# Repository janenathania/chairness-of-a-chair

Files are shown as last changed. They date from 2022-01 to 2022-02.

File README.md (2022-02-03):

# CHAIRNESS OF A CHAIR
## Hochschule Augsburg - Interactive Media - 5th Semester - Wicked Things

This repository contains source of codes and informations about the hardwares and its hacking. Everything that is needed to hack a hoverboard and control it with Arduino and Processing to make a fully functional remote controlled moving chair can be found here. Some codes and methods are taken from other GitHub Repositories as well, the link will be provided in in the description.

## TABLE OF CONTENT
- [HARDWARE](https://github.com/janenathania/chairness-of-a-chair/blob/main/README.md#hardware)
- [FLASHING](https://github.com/janenathania/chairness-of-a-chair/blob/main/README.md#flashing)
- [SERIAL INTERFACE](https://github.com/janenathania/chairness-of-a-chair/blob/main/README.md#serial_interface)
- [ARDUINO](https://github.com/janenathania/chairness-of-a-chair/blob/main/README.md#arduino)
- [PROCESSING](https://github.com/janenathania/chairness-of-a-chair/blob/main/README.md#processing)
- [PROTOTYPE](https://github.com/janenathania/chairness-of-a-chair/blob/main/README.md#prototypes)
- [3D PRINT](https://github.com/janenathania/chairness-of-a-chair/blob/main/README.md#3d_print)

## HARDWARE

For this project we use the older version of the hoverboard that only has one chip to control both side of the hoverboard.
The main model of the chip is STM32F103. 

 

Further information and instruction can be found in a GitHub Repository by lucysrausch <br/>
https://github.com/lucysrausch/hoverboard-firmware-hack

## FLASHING

In order to control the hoverboard we have to hack the firmware first. Fristly we have to erase every progamms that are built in the hoverboard.
The method is called flashing. There are several methods to do the flashing

We follow the whole procedure from this website <br/>
http://bauhausinteraction.org/opl/how-to-control-a-hoverboard-with-an-arduino/

And more detailed instructions can be found from this GitHub repository
The Method that we follow to make this project is `VARIANT_USART` <br/>
https://github.com/EFeru/hoverboard-firmware-hack-FOC

## SERIAL INTERFACE
### ESP Code

Parts used:
- Hoverboard with STM32F103 chip
- ESP8266
- DC/DC Converter
- Wireless Router (we use tp-link TL-MR3020)

If you are using a ESP for the first time, follow these instructions to get ready to use it: https://randomnerdtutorials.com/how-to-install-esp8266-board-arduino-ide/

Then import these two libraries to your Arduino IDE:
- Ramp for motors https://github.com/siteswapjuggler/RAMP
- Protocoll for wireless communication between Processing and ESP https://sojamo.de/libraries/oscP5/network

You need a Wireless Router with an AP Mode. In the Code you have to change the SSID and PWD into your own password for the router
If you are building two chairs like us, you might have to change the last digit of the IPAddress for the second ESP
Each Chair requires 1 ESP and the IPAdress should be different from each other

`const IPAddress ip(192, 168, 1, 202); change the 202 to 203.`



After that you can upload our ESP-Code to your ESP. 

### ESP Build

Disconnect the Sideboard which is on the side of the mainboard. Take your ESP and DC Converter and connect everything like this:
- 15V red wire goes to the left wire of the converter, which is labeled with `in`
- TX blue wire goes to the RX pin of the ESP
- RX green wire goes to the TX pin of the ESP
- GND black wire goes to the middle wire of the converter with the `ground` label
- connect another black wire to the middle wire of the converter and put it on the GND pin on the ESP
- the last wire of the converter (adjust 5V out) goes to the Vin pin of the ESP 



Original Links of the images <br/>
- https://m.media-amazon.com/images/I/51Z9NoCxWwL._SL1000_.jpg
- https://wiki.volkszaehler.org/_media/hardware/controllers/amica-nodemcu-esp8266-lua-cp2102-wifi-development-module-iot-gujarat.png
- https://github.com/EFeru/hoverboard-firmware-hack-FOC/blob/master/docs/pictures/mainboard_pinout.png

## ARDUINO

Parts used:
- 1x Arduino Uno
- 1x Seedstudio Grove Shield
- 2x Seedstudio Grove Joystick

Our Code is able to steer two hoverboards at the same time.

We used an Arduino Uno with the Seedstudio Grove Shield on top and we connect the first Seedstudio Grove Joystick to the A0 and the second Joystick to the A2 Connector of the Grove Shield.

We send the coordinates of the Joysticks as a string over the serial port.

GitHub Repository from HybridThingsLab <br/>
https://github.com/HybridThingsLab/wicked-things-2021/tree/main/01_playground/Arduino

## PROCESSING

Processing is able to read the data from the Arduino and send it over WLAN to the ESP.

To make sure that everything is working correctly you need use Processing 4 as the software.

Open the processing code (that you can find in the folder above) and connect your arduino to your pc. Run the code and check if there is an error. If so that means the code uses the wrong usb port. Check the number of your port on which your arduino is connected to and change it in the code.



If there are two squares and you can move them with the joysticks, then everything is working fine.

Now start the hoverboard and connect the Wlan of your PC with the Router and run the processing code .

If everything is correct, your hoverboard should move if you use the joysticks.



GitHub Repository from HybridThingsLab <br/>
https://github.com/HybridThingsLab/wicked-things-2021/tree/main/01_playground/Processing

## PROTOTYPES

To ensure that the chair is safe to ride we have done some experiments on the shape of the chair and the supporting board the is built between the hoverboard and the actual chair.

  

The board acts not only as a support that connect hoverboard and the chair, but also as a place to put the motherboard that control the whole thing.

  

The final design of the chair. The shape of the chair is chosen after several user tests to decide which shape is the safest to ride on. The important feature of the moving chair is its backrest. It is to protect the user from falling over during sudden movement of the chair.
The board at the bottom is made quite broad. It is made like that to make sure that the user has enough space to place their feet on it and feel sturdy while sitting on the chair. The board itself has in total 5 wheels. 2 wheels are from the hoverboard that can move following the controllers input and the other 3 wheels are the supporting wheels (2 in front and 1 at the back) to make sure that the whole chair doesn't flip over during sudden movement or sudden break.

## 3D PRINT

This is our extra parts. We make the cover for controllers, Arduino and ESP with 3D Print. You can make it with anything you like. But we attached the raw files of the 3D Models so you can try to 3D Print it if you have a 3D Printer.

  

The controller are made main from an arudino joystick kit and it is covered with a 3D printed cover. To make it a cleaner look and more rigid body. It makes the controller easier to hold it and comfortable while using it, so that the controllers can controll the chair precisely. <br/>



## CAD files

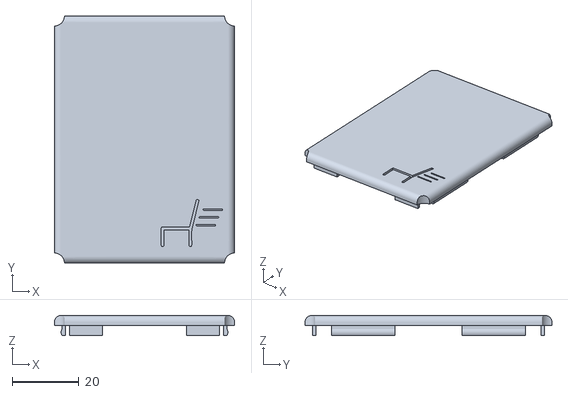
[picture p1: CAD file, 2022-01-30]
3D Print/esp_box_deckel.stl
54.0 x 74.0 x 6.00

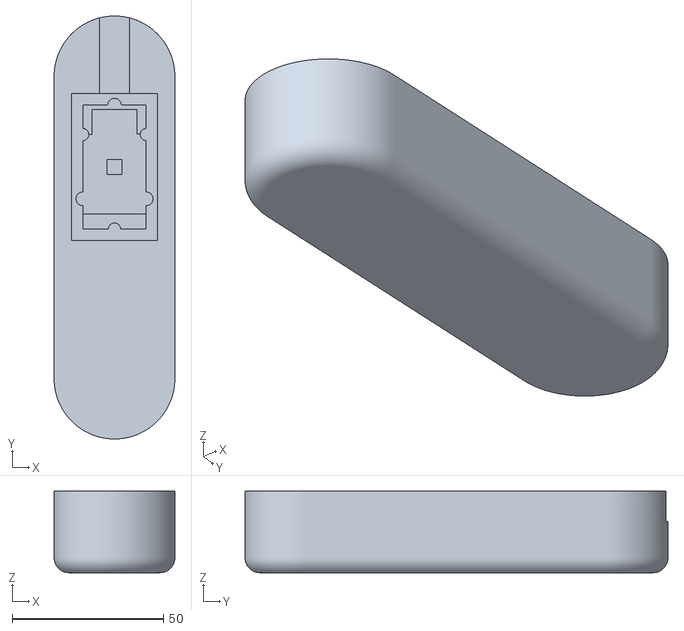
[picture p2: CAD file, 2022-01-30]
3D Print/joystick_box_base.stl
40.0 x 140.0 x 27.0

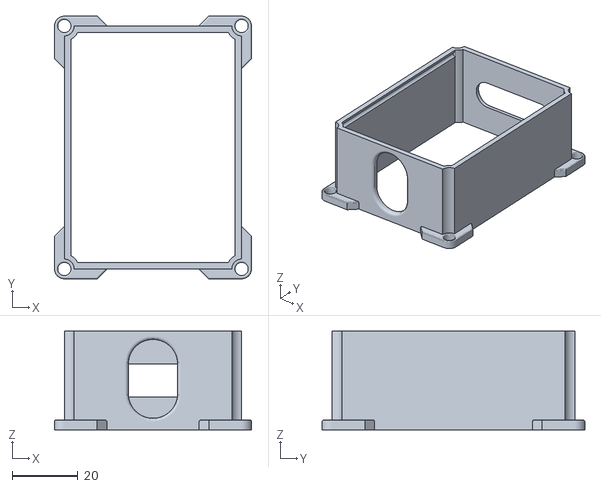
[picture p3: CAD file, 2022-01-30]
3D Print/esp_box.stl
60.0 x 80.0 x 30.0

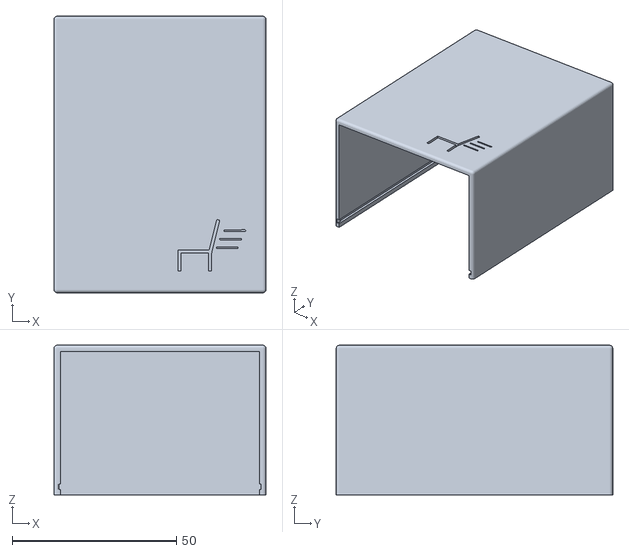
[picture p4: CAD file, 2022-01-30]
3D Print/arduino_box_lid.stl
64.6 x 84.3 x 45.6

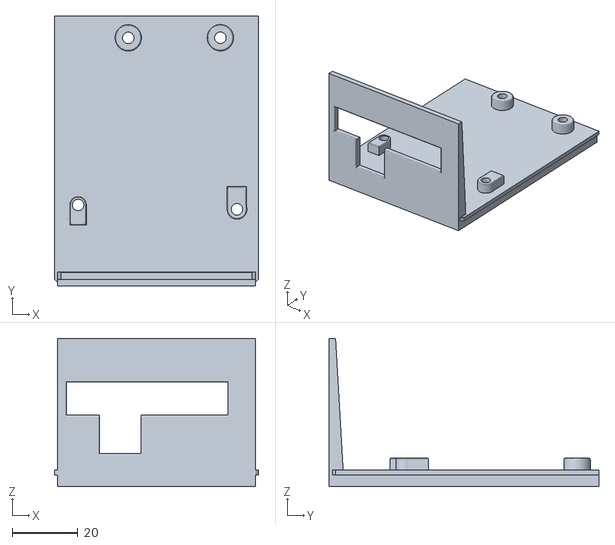
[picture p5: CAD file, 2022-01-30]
3D Print/arduino_box_base.stl
62.0 x 82.0 x 45.0

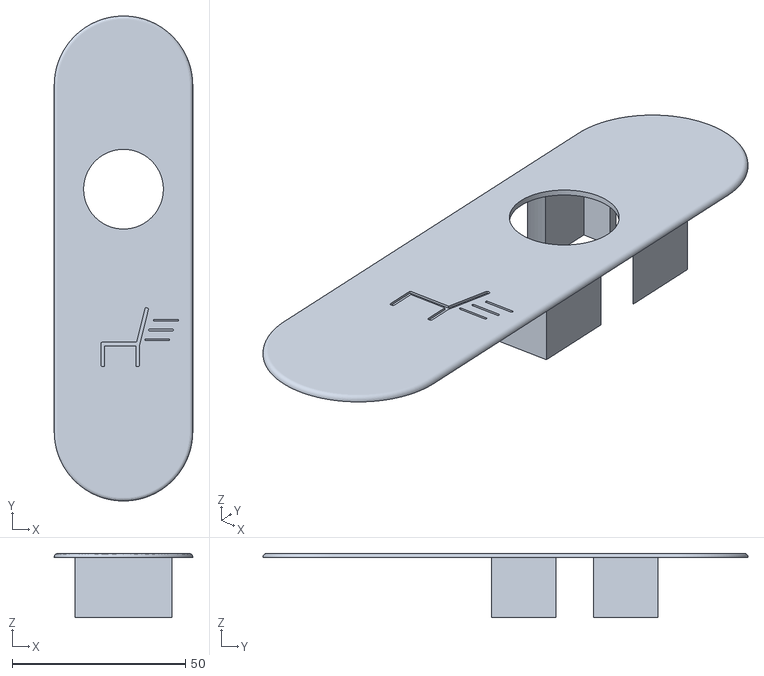
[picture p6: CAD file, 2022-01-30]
3D Print/joystick_box_lid.stl
40.0 x 140.0 x 18.5

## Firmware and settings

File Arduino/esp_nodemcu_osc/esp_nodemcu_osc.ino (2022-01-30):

// *******************************************************************
//  based on Arduino Nano 5V example code
//  for   https://github.com/EmanuelFeru/hoverboard-firmware-hack-FOC
//  Copyright (C) 2019-2020 Emanuel FERU <aerdronix@gmail.com>
//
// *******************************************************************

// ########################## DEFINES ##########################
#define SERIAL_BAUD         115200     // [-] Baud rate for built-in Serial (used for the Serial Monitor)
#define START_FRAME         0xABCD       // [-] Start frme definition for reliable serial communication
// #define DEBUG_RX                        // [-] Debug received data. Prints all bytes to serial (comment-out to disable)

// interval control hoverboard
unsigned long lastSent = 0;
int updateSent = 10; // interval to send value via serial port

// osc library
#include <ArduinoOSC.h> // https://github.com/hideakitai/ArduinoOSC

// WiFi stuff
const char* ssid = "maschinenraum";
const char* pwd = "maschinenraum";
const IPAddress ip(192, 168, 1, 202); // set unique IP (last number e.g. 200) for each robot here!!!
const IPAddress gateway(192, 168, 1, 1);
const IPAddress subnet(255, 255, 255, 0);

// for ArduinoOSC
const int recv_port = 9999;
const int send_port = 8888;

// include ramp library, https://github.com/siteswapjuggler/RAMP
#include <Ramp.h>
// parameters ramp
rampInt steer_motors;
rampInt speed_motors;
int ramp_time = 150; // time interpolation ramp in milliseconds

// serial command
typedef struct {
  uint16_t start;
  int16_t  steer;
  int16_t  speed;
  uint16_t checksum;
} SerialCommand;
SerialCommand Command;


//heartbeat variables
long lastheartbeat = 0;
#define HEARTBEAT_TIMEOUT_MS 250


// ########################## SETUP ##########################
void setup()
{

  // serial
  Serial.begin(SERIAL_BAUD);


  // WiFi stuff
  WiFi.begin(ssid, pwd);
  WiFi.config(ip, gateway, subnet);
  while (WiFi.status() != WL_CONNECTED) {
    delay(500);
  }

  // osc messages
  OscWiFi.subscribe(recv_port, "/control", [](OscMessage & m) {
    control(m);
  });

  //register a new OSC message for heartbeat a according function
  OscWiFi.subscribe(recv_port, "/heartbeat", [](OscMessage & m){
    heartbeat(m);
  });



}

// ########################## SEND ##########################
void Send(int16_t uSteer, int16_t uSpeed)
{
  // Create command
  Command.start    = (uint16_t)START_FRAME;
  Command.steer    = (int16_t)uSteer;
  Command.speed    = (int16_t)uSpeed;
  Command.checksum = (uint16_t)(Command.start ^ Command.steer ^ Command.speed);

  // Write to Serial
  Serial.write((uint8_t *) &Command, sizeof(Command));
}



// ########################## LOOP ##########################

void loop(void) {

  // should be called to parse incoming OSC messages
  OscWiFi.parse();

  // update ramp
  steer_motors.update();
  speed_motors.update();

  // Do not try to send Serial stuff too often, be prevent this by checking when we sent the last time
  if ((millis() - lastSent) > updateSent) {
    // control hoverboard (steering, speed) > -1000 to 1000
    Send(steer_motors.getValue(), speed_motors.getValue());
    // update timestamp last sent
    lastSent = millis();
  }

  //check if we still got a heartbeat
  if(lastheartbeat + HEARTBEAT_TIMEOUT_MS < millis()){
    emergencyStop();
  }


}

// ########################## OSC  ##########################

void control(OscMessage m) {

  // steer
  int steer = m.arg<int>(0);

  // speed
  int speed = m.arg<int>(1);

  // update ramp
  steer_motors.go(steer, ramp_time);
  speed_motors.go(speed, ramp_time);

}

void emergencyStop(){
  Send(0, 0);
}

//heartbeat received
void heartbeat(OscMessage m) {
  lastheartbeat = millis();
}

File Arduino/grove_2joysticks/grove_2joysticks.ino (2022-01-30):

/*
  Thumb Joystick demo v1.0
  by:https://www.seeedstudio.com
  connect the module to A0&A1 for using;
*/

// serial output
unsigned long lastSent = 0;
int updateSerial = 10; // interval to send value via serial port

void setup()
{
  Serial.begin(57600);
}

void loop()
{

  // read joystick 1
  int sensorValue1 = analogRead(A0);
  int sensorValue2 = analogRead(A1);

  // read joystick 2
  int sensorValue3 = analogRead(A2);
  int sensorValue4 = analogRead(A3);
  

  // Do not try to send Serial stuff too often, be prevent this by checking when we sent the last time
  if ((millis() - lastSent) > updateSerial) {
    // send values to serial port
    Serial.print(sensorValue2);
    Serial.print(" ");
    Serial.print(sensorValue1);
    Serial.print(" ");
    Serial.print(sensorValue4);
    Serial.print(" ");
    Serial.println(sensorValue3);
    // update timestamp last sent
    lastSent = millis();
  }

}
